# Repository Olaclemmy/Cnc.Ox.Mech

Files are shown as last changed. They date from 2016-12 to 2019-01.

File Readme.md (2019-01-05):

# Readme

## Overview

This is a 3D Cad Solidworks model of the Ox CNC from Ooznest with the modified plates

Most of the design is held together via M5 nuts, but some of the brackets are using drop in M4 T Nuts
just because this is what i had spare at the time

## TODO

### Motor cover

  * https://www.thingiverse.com/thing:1002246/files

### Z Axis End stop

I need to merge in a design between the Z Axis End stop and the cable chain

### Spindle gear down

consider a 1/8 belt driven gear down of the spindle for milling metal

### Parts

For the motor mount, typically the brackets for 2.2Kw motors are about 12mm thick, which is the same as the mdf I'm using
so I should be able to fasten on brackets for Max Z Height on the same plane as the spindle, and other tools besides

  * The bolt spacing is 60mm for connecting parts to the spolier board
    add to spoiler board design
  * hole diameter is 7mm for the spoiler board because of the fasteners underneath
    and 6mm for the stock as that is the size of the bolts

  * Design brackets for the dremmel to raise it up more

### Cable Chain

Need to play this one by ear, I Think the cable chain may have problems bending at the angle I need maybe

  * Check the pilot hole sizes for the self tappers used in the cablechain brackets on the Y and X Axis
  * Finish the 2nd part of the cablechain bracket (the one that fastens to the moving Y Axis gantry)
  * cable chain outer diameter is 110mm approx

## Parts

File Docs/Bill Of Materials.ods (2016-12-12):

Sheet: OpenBuild
X Axis
 | Available | Used
Nylon Insert Nuts - 5mm (http://openbuildspartstore.com/nylon-insert-hex-locknut/) | 2
Low Profile Screws Singles - 25mm (http://openbuildspartstore.com/low-profile-screws-m5/) | 6
Tee Nuts - M5 (Singles) (http://openbuildspartstore.com/tee-nuts-25-pack/) | 16
Aluminum Spacers - 6mm (http://openbuildspartstore.com/aluminum-spacers/) | 3
Aluminum Spacers - 40mm (http://openbuildspartstore.com/aluminum-spacers/) | 2
Low Profile Screws Singles - 10mm (http://openbuildspartstore.com/low-profile-screws-m5/) | 12
1/4" x 8m Flexible Coupling (http://openbuildspartstore.com/1-4-x-8mm-flexible-coupling/) | 1
Aluminum Spacers - 3mm (http://openbuildspartstore.com/aluminum-spacers/) | 2
Slot Washers (http://openbuildspartstore.com/slot-washer-15x5x2mm/) | 8
Eccentric Spacers - 6mm Full Size Wheels (http://openbuildspartstore.com/eccentric-spacer/) | 3
Xtreme Solid Wheel Kit (http://openbuildspartstore.com/xtreme-solid-v-wheel-kit/) | 6
Cast Corners (http://openbuildspartstore.com/cast-corner-bracket/) | 4
V-Slot Gantry Plate (Universal) (http://openbuildspartstore.com/v-slot-gantry-plates/) | 1
Low Profile Screw - Singles - 20mm (http://openbuildspartstore.com/low-profile-screws-m5/) | 10
Low Profile Screws - Singles - 55mm (http://openbuildspartstore.com/low-profile-screws-m5/) | 2
Ball Bearing 688Z 8x16x5 (http://openbuildspartstore.com/ball-bearing-688z-8x16x5/) | 2
8mm Shim (http://openbuildspartstore.com/8mm-shim/) | 2
Lock Collar - 8mm (http://openbuildspartstore.com/lock-collar/) | 2
C-Beam End Mount (http://openbuildspartstore.com/c-beam-end-mount/) | 2
Anti Backlash Nut Block (http://openbuildspartstore.com/anti-backlash-nut-block-for-8mm-metric-acme-lead-screw/) | 1
Y Axis
Nylon Insert Nuts - 5mm (http://openbuildspartstore.com/nylon-insert-hex-locknut/) | 2
Low Profile Screws Singles - 25mm (http://openbuildspartstore.com/low-profile-screws-m5/) | 4
Tee Nuts - M5 (Singles) (http://openbuildspartstore.com/tee-nuts-25-pack/) | 8
Aluminum Spacers - 6mm (http://openbuildspartstore.com/aluminum-spacers/) | 10
Aluminum Spacers - 40mm (http://openbuildspartstore.com/aluminum-spacers/) | 2
Low Profile Screws Singles - 10mm (http://openbuildspartstore.com/low-profile-screws-m5/) | 4
Low Profile Screws Singles - 30mm (http://openbuildspartstore.com/low-profile-screws-m5/) | 4
1/4" x 8m Flexible Coupling (http://openbuildspartstore.com/1-4-x-8mm-flexible-coupling/) | 1
Aluminum Spacers - 3mm (http://openbuildspartstore.com/aluminum-spacers/) | 2
Eccentric Spacers - 6mm Full Size Wheels (http://openbuildspartstore.com/eccentric-spacer/) | 2
Xtreme Solid V Wheel Kit (http://openbuildspartstore.com/xtreme-solid-v-wheel-kit/) | 4
Cast Corners (http://openbuildspartstore.com/cast-corner-bracket/) | 4
Build Plate (http://openbuildspartstore.com/build-plate/) | 1
Self Tapping Screws (http://openbuildspartstore.com/self-tapping-screw/) | 8
Low Profile Screws - Singles - 20mm (http://openbuildspartstore.com/low-profile-screws-m5/) | 10
Low Profile Screws - Singles - 55mm (http://openbuildspartstore.com/low-profile-screws-m5/) | 2
Ball Bearing 688Z 8x16x5 (http://openbuildspartstore.com/ball-bearing-688z-8x16x5/) | 2
8mm Shim (http://openbuildspartstore.com/8mm-shim/) | 2
Lock Collar - 8mm (http://openbuildspartstore.com/lock-collar/) | 2
C-Beam End Mount (http://openbuildspartstore.com/c-beam-end-mount/) | 2
Anti Backlash Nut Block (http://openbuildspartstore.com/anti-backlash-nut-block-for-8mm-metric-acme-lead-screw/) | 1
Z Axis
C-Beam Linear Actuator Bundle (http://openbuildspartstore.com/c-beam-linear-actuator-bundle/) | 1
Low Profile Screws Singles - 10mm (http://openbuildspartstore.com/low-profile-screws-m5/) | 8
1/4" x 8m Flexible Coupling (http://openbuildspartstore.com/1-4-x-8mm-flexible-coupling/) | 1
Black Angle Corner Connectors (http://openbuildspartstore.com/black-angle-corner-connector/) | 4
Low Profile Screw - Singles - 20mm (http://openbuildspartstore.com/low-profile-screws-m5/) | 10
OpenBuilds Spindle Mount (http://openbuildspartstore.com/router-spindle-mount/) | 1
Frame
Tee Nuts - M5 (Singles) (http://openbuildspartstore.com/tee-nuts-25-pack/) | 44
Low Profile Screws Singles - 8mm (http://openbuildspartstore.com/low-profile-screws-m5/) | 24
Low Profile Screws Singles - 10mm (http://openbuildspartstore.com/low-profile-screws-m5/) | 26
Drop In Tee Nuts (http://openbuildspartstore.com/drop-in-tee-nuts/) | 2
Cast Corners (http://openbuildspartstore.com/cast-corner-bracket/) | 18
Single L Brackets (http://openbuildspartstore.com/l-bracket/) | 2
90 Degree Joining Plate (http://openbuildspartstore.com/90-degree-joining-plate/) | 2
Self Tapping Screws (http://openbuildspartstore.com/self-tapping-screw/) | 6
M4 x 6mm Screws (http://openbuildspartstore.com/socket-head-cap-screw-m4/) | 2
C-Beam Linear Rail - 500mm (http://openbuildspartstore.com/c-beam-linear-rail/) | 2
8mm Metric Acme Lead Screw - 500mm (http://openbuildspartstore.com/8mm-metric-acme-lead-screw/) | 2
500mm 20x60 V-Slot (http://openbuildspartstore.com/v-slot-linear-rail/) | 6

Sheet: Electronics
http://3dtek.xyz/blogs/technical-docs/19171599-shapeoko-vs-x-carve-vs-heavy-mill-choosing-a-cnc-router
C Beam machine
 | Qty | Cost | Cost x Qty | Vat
C Beam machine + Motors | 1 | 360.24 | 360.24 | 432.29
CNC xPRO V2 | 1 | 82.88 | 82.88 | 99.46
Power Supply 24V | 1 | 31.88 | 31.88 | 38.26
Bosch Colt Router | 1 | 170 | 170 | 170
End Caps | 12 | 1.18 | 14.16 | 16.99
Slot Cover / Panel Holder – 500mm | 10 | 1.28 | 12.8 | 15.36
 |  |  | 671.96 | 772.35
X Carve Machine
Xcarve Bundle, includes 300W spindle and PSU, mill and clamp bits | 1 | 593.85 | 593.85 | 712.62
CNC xPRO V2 | 0 | 82.88 | 0 | 0
G Shield for Arduino | 0 | 55 | 0 | 0
Main issue is delivery costs |  |  |  | 712.62
which would mean getting it from robosavvy instead
http://robosavvy.com/store/x-carve-basic-kit-plus.html
Ox CNC (current favourite)
http://ooznest.co.uk/3D-Printer-CNC-Kits-Bundles/OX-CNC-Mechanical-Kit
Ooznest OX CNC Mechanical Kit 500 x 750mm black | 1 | 657.5 | 657.5 | 657.5
+ NMEA 23 Motors
24V 360W Power Supply | 1 | 25 | 25 | 25
Hall Effect Endstop | 3 | 7 | 21 | 21
Premium RAMPS 1.4 Controller Board + 5 x st controller | 1 | 55 | 55 | 55
OX CNC Router Mounting Add-On Kit | 0 | 48 | 0 | 0
dewalt router 620w D26200 | 0 | 150 | 0 | 0
http://www.amazon.co.uk/DeWalt-D26200-Compact-Router-DEWD26200/dp/B004ISXKC0
LJ12A3-4-Z/BX inductive sensor (accuracy?) | 1 | 4.57 | 4.57 | 4.57
we want NC or normally closed to detect wiring faults
http://www.amazon.co.uk/LJ12A3-4-Z-2-wire-Tubular-Inductive-Proximity/dp/B00EL0TPE2
Get Bracket for Dremmel (4 corner bits)
Look into Z axis clearance |  |  |  | 763.07
flex chain guard
fan for ramps board
Wiring – check youtube
It looks like the ramps board is configured for 12V by default
for 24V we would need to change some components on it and use the Taurino Power, which is an arduino configured for higher voltages
so I've decided instead to build a custom Ramps board for the Arduino due with logic conversions that takes DRV8825 polulu modules

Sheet: Sheet1
Description | Qty | Unit (£) | Total (£) | Link | Qty Needed | Notes
Material
Hobbarts 9mm Panel LaserPly 800x450 | 0 | 9 | 0 | https://hobarts.com/sheet-materials/wood/wood:-laserply-birch-plywood_124_15_56/9mm-laser-grade-birch-plywood-p-392.html
Black Acrylic Sheet 600 x 400 | 0 | 7.15 | 0 | https://hobarts.com/sheet-materials/acrylic/acrylic-sheet-solid-colours_124_7_4/3mm-black-cast-acrylic-p-906.html
GT2 Timing Belt – 2meters | 0 | 4.49 | 0 | http://www.amazon.co.uk/Meters-Timing-Printing-Printer-Reprap/dp/B00WR9993Q
 |  |  |  | TODO check how much of the above is needed
Electronics
Arduino Due | 0 | 38 | 0 | http://www.amazon.co.uk/367/dp/B00A6C3JN2 |  | TODO replace this with custom board
TODO Stepper Controllers
Stepper Motor Driver | 0 | 11.74 | 0 | https://www.sparkfun.com/products/12779 |  | TODO replace this with custom board
AS5048 Encoder | 0 | 5.18 | 0 | http://www.digikey.com/product-detail/en/AS5048B-HTSP-500/AS5048B-HTSP-500TR-ND/3188616
Magnet for Encoder | 0 | 0.85 | 0 | http://www.ams.com/eng/Products/Position-Sensors/Magnets/AS5000-MD6SH-1
Open Build Parts
270mm x 165mm x 12mm Aluminium Plate | 0 | 19.15 | 0 | http://www.ebay.co.uk/itm/270mm-x-165mm-x-12mm-Aluminium-Plate-Sheet-Grade-6082-T651-HE30/261885689580 |  | This should cover the end plates for the C Beam, and leave 120 x 160 spare
Xtreme mini Wheel Kit | 0 | 3.25 | 0 | http://openbuildspartstore.com/xtreme-mini-v-wheel-kit/?page_context=category&faceted_search=0
Delrin mini Wheel Kit | 0 | 2.13 | 0 | http://openbuildspartstore.com/delrin-mini-v-wheel-kit/?page_context=category&faceted_search=0
Black V-Slot Linear Rail 20x40 500mm | 1 | 4.66 | 4.66 | http://openbuildspartstore.com/black-v-slot-linear-rail/?page_context=brand&faceted_search=0
Black V-Slot Linear Rail 20x60 500mm | 2 | 5.54 | 11.08 | http://openbuildspartstore.com/black-v-slot-linear-rail/?page_context=brand&faceted_search=0
C-Beam Linear Rail 250mm | 0 | 4.56 | 0 | http://openbuildspartstore.com/c-beam-linear-rail/?page_context=brand&faceted_search=0
C-Beam Linear Rail 500mm | 0 | 9.13 | 0 | http://openbuildspartstore.com/c-beam-linear-rail/?page_context=brand&faceted_search=0
C-Beam Gantry Plate | 0 | 6.13 | 0 | http://openbuildspartstore.com/c-beam-gantry-plate/?page_context=category&faceted_search=0
C-Beam End Mount | 0 | 5.7 | 0 | http://openbuildspartstore.com/c-beam-end-mount/?page_context=category&faceted_search=0
 |  |  | 15.74 | Grand Total
Robot Digg
Anti-backlash Nut for Tr8*8 Leadscrew | 1 | 7.72 | 7.72 | http://www.robotdigg.com/product/18/Anti-backlash-Nut-for-Tr8*8-Leadscrew
Bearings / Rods
Linear Rod M8mm x 600mm | 0 | 5.5 | 0 | http://www.amazon.co.uk/Stainless-Steel-Rod-Round-600mm/dp/B00C2PTPC0
Threaded Rod M8mm x 500mm 2 pack | 0 | 3.49 | 0 | http://www.wickes.co.uk/Wickes-Threaded-Rod-M8x500mm-Pack-2/p/511122
Radial Ball Bearings 608ZZ Set of 4 | 0 | 5.39 | 0 | https://www.adafruit.com/products/1178 | 3 | Model used on Solidworks = ISO 108, 22mm outer diameter, 8mm inner diameter, 7mm thick
Linear Bearing 8mm LM8UU x10 | 0 | 6.99 | 0 | http://www.amazon.co.uk/gp/product/B009HW409O?psc=1&redirect=true&ref_=oh_aui_detailpage_o00_s00 | 4 | with Cheap chinese ones, some will be duds, adafruit provide best ones
Linear Bearing 8mm LM8UU | 0 | 2.29 | 0 | https://www.adafruit.com/products/1181
GT2 Pulley 20tooth 8mm bore | 0 | 1.57 | 0 | http://www.robotdigg.com/product/23/GT2-Pulley-20-Teeth-8mm-Bore
Motors
Stepper Motor | 0 | 11.59 | 0 | https://www.sparkfun.com/products/9238 | 1 | 200 Steps NEMA-17
Stepper Motor Mount / Screws | 0 | 6.94 | 0 | https://www.adafruit.com/products/1297 | 1
Stepper Coupler 5mm – 8mm | 0 | 3.84 | 0 | https://www.adafruit.com/products/1176 | 1
Screws / Nuts |  |  |  |  |  | Sourced from DBA Hardware / Bolt Base
Socket Head Bolts – M3 x 40mm len x 20 | 0 | 2.16 | 0 | http://www.amazon.co.uk/Bolt-Base-Stainless-Steel-Socket/dp/B00B3RLEHM | 14
Socket Head Bolts – M3 x 20mm len x 20 | 0 | 0.32 | 0 | http://www.amazon.co.uk/Socket-Bolts-Stainless-Screws-Delivery/dp/B00A6YUCQC | 12
Socket Head Bolts – M3 x 8mm len x 16 | 0 | 1.93 | 0 | http://www.amazon.co.uk/Tensile-Button-Setscrew-Socket-Screws/dp/B00HUVT3SM | 12
LockNuts – M3 x 50 | 0 | 1.99 | 0 | http://www.amazon.co.uk/Nyloc-Nylon-Insert-Stainless-Delivery/dp/B00A6ED8MM | 30
Washers – M3 x 7mm dia x 50 | 0 | 1.68 | 0 | http://www.amazon.co.uk/Washer-3-2mm-Stainless-Washers-Delivery/dp/B00A6PGHC4 | 60 | In solidworks used ISO Washer 7092 SmallGrade
Socket Head Bolts – M4 x 20mm len x 20 | 0 | 1.62 | 0 | http://www.amazon.co.uk/Button-Screws-Stainless-Socket-Delivery/dp/B00A7BUO1C | 4
Washers – M4 x 9mm dia x 50 | 0 | 1.55 | 0 | http://www.amazon.co.uk/Washer-4-3mm-Stainless-Washers-Delivery/dp/B00A6PILR8 | 8
Nuts – M4 x50 | 0 | 1.4 | 0 | http://www.amazon.co.uk/Full-Stainless-Steel-Hexagon-Delivery/dp/B00A6G5H0G | 4
Washers – M8 x 16dia x 50 | 0 | 1.95 | 0 | http://www.amazon.co.uk/Washer-8-4mm-Stainless-Washers-Delivery/dp/B00A6PS2QI | 4 | In solidworks used ISO Washer 7091 NormalGrade
LockNuts – M8 x20 | 0 | 2.2 | 0 | http://www.amazon.co.uk/Nyloc-Nylon-Insert-Stainless-Delivery/dp/B00A6FI2GS | 1
Nuts – M8 x20 | 0 | 1.85 | 0 | http://www.amazon.co.uk/Full-Stainless-Steel-Hexagon-Delivery/dp/B00A6GAIC8 | 6
Assorted Springs (need 2 x 8mm) | 0 | 9.99 | 0 | http://www.clasohlson.com/uk/Assorted-Springs/31-2132 | 2
Assembly A – Xaxis
Socket Head Bolts – M3 x 40mm len | 0 |  |  | Fasteners
LockNuts – M3 | 0 |  |  | Fasteners
Washers – M3 x 7mm dia | 0 |  |  | Fasteners
Washers – M8 x 15.5dia | 0 |  |  | Anti-Backlash
Assorted Springs 8mm | 0 |  |  | Anti-Backlash
Linear Bearing 8mm LM8UU | 0 |  |  | Axis
Nuts – M8 | 0 |  |  | Axis
Assembly D – Xaxis Base
Socket Head Bolts – M3 x 20mm len | 0 |  |  | Fasteners
LockNuts – M3 | 0 |  |  | Fasteners
Washers – M3 x 7mm dia | 0 |  |  | Fasteners
Radial Ball Bearings 608ZZ | 0 |  |  | Axis
LockNuts – M8 | 0 |  |  | Axis
Nuts – M8 | 0 |  |  | Axis
Assembly D – Stepper Mount
Socket Head Bolts – M3 x 8mm len | 0 |  |  | Stepper Bracket
Washers – M3 x 7mm dia | 0 |  |  | Stepper Bracket
Socket Head Bolts – M4 x 20mm len | 0 |  |  | Stepper Bracket
Washers – M4 x 9mm dia | 0 |  |  | Stepper Bracket
Nuts – M4 | 0 |  |  | Stepper Bracket
Assembly D – Pulley Mount1
Socket Head Bolts – M3 x 40mm len | 0 |  |  | Fasteners
Washers – M3 x 7mm dia | 0 |  |  | Fasteners
LockNuts – M3 | 0 |  |  | Fasteners
Nuts – M8 | 0 |  |  | Axis
Radial Ball Bearings 608ZZ | 0 |  |  | Axis
GT2 Pulley 20tooth 8mm bore | 0 |  |  | Axis
 |  |  | 39.2 | Grand Total
Links
http://www.diydata.com/information/screwholes/screwholes.php
http://www.trfastenings.com/pages/Tapping+Sizes+and+Clearance+Holes
https://docs.google.com/spreadsheets/d/1oVcTCycR9qHi5JeS0x5Of-aC_XsIiMkX0GsWGpkmOUA/edit#gid=0
http://uk.mouser.com/new/ams/ams-as5048-sensor/
http://handycrowd.com/screws-explained-gauge-size-pilot-holes-and-wall-plugs/
http://www.bwc.com/shop/dualvee-single-edge-track.html

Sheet: Sheet2
200 steps = 1.8 degrees
http://reprap.org/wiki/Step_rates
http://prusaprinters.org/calculator/
Steps per rotation |  |  | 200.00000000
Degrees per step |  |  | 1.80000000
Actuation Type | Full Steps per mm | Micro Stepping Ratio(2/4/8) | Steps per mm | Full rotation / distance mm | Distance per step mm
GT2 20 tooth pulley | 5.00000000 | 1 | 5.00000000 | 40.00000000 | 0.20000000
GT2 30 tooth pulley | 3.33000000 | 1 | 3.33000000 | 60.06006006 | 0.30030030
standard 8mm threaded rod | 160.00000000 | 1 | 160.00000000 | 1.25000000 | 0.00625000
OpenBuilds 8mm Metric Acme Lead Screw | 100.00000000 | 1 | 100.00000000 | 2.00000000 | 0.01000000
The C-Type Extrusion 250mm length
without holes, has a Mass of 220g
Volume 219361.10 cubic millimeters
1 can = 15g, so about 15cans
green sand is typically used for casting
Have the X Axis independant of the Y Axis
i.e. have the part moved backwards and forwards
to allow the part to be brought forward after printing, and to avoid accumilation of inaccuracy for multiple axis
also should allow for greater speed for 3d printing
only down side is that larger parts may be difficult to move, but this is only a mid sized device
http://forums.reprap.org/read.php?177,67307
I think a similar design to the K8200 axis arrangement is the best, but with the X Axis in motion
Y Axis (Front to Back) should be at the bottom fixed to the frame
Z Axis (Top to Bottom) should have 2 gantrys attached to the main frame
X Axis (Left to Right) should be attached to the Z Axis
Optional idea to attach the Y Axis to the Z Gantry for CNCing a big area
It turns out the weight on the Y Axis (front to back) can affect the speed / profile, so a weight sensor on the bed might be useful
Change in Speed | 0.2 | m/s
Time | 0.1 | Seconds
Mass | 0.5 | Kg
Acceleration | 2 | m/s2
Force Movement | 1 | Newtons
Force Movement | 0.1 | Kg
Cost of 8mm 500mm Leadscrew and anti-backlash nut is around £18-20
Option 1 500mm threaded rod from wicks
Option 2 500mm ballscrew
http://www.alibaba.com/product-detail/precision-ball-screw-sfu1605-for-cnc_60224722736.html?s=p
http://www.cnczone.com/forums/linear-and-rotary-motion/261308-affordable-8mm-diameter-ball-screws.html

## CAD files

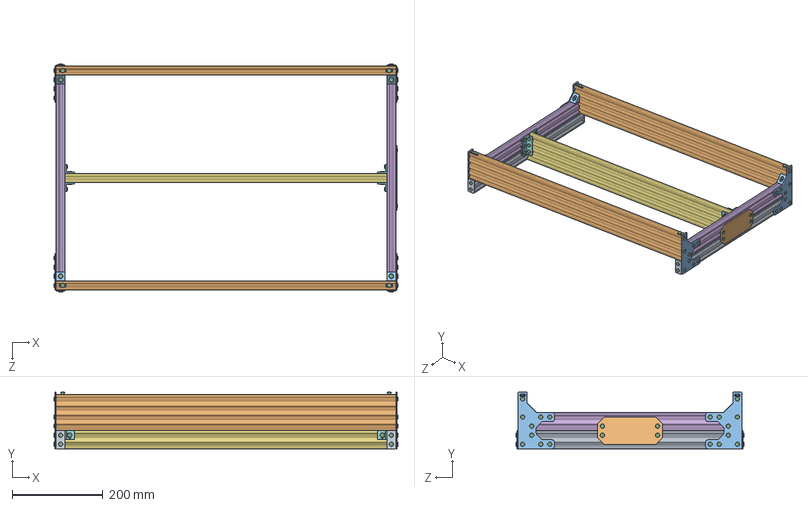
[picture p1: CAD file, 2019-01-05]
Assemblies/Base/Base-Frame.SLDASM
759.5 x 125.0 x 503.5 mm
V-Slot 20x40-Base-494 x 2
V-Slot 20x80-Base-750 x 2
Y-End-Plate x 4
5mm Low Profile Socket Head Screw x 84
T-Nut-M5-Slidein x 68
V-Slot 20x40-Base-454 x 2
V-Slot 20x80-Base-710
Universal L Bracket - Triple x 4
EndPlate x 4
Ooznest-FacePlate
90 Degree Angle Corner Connector x 4

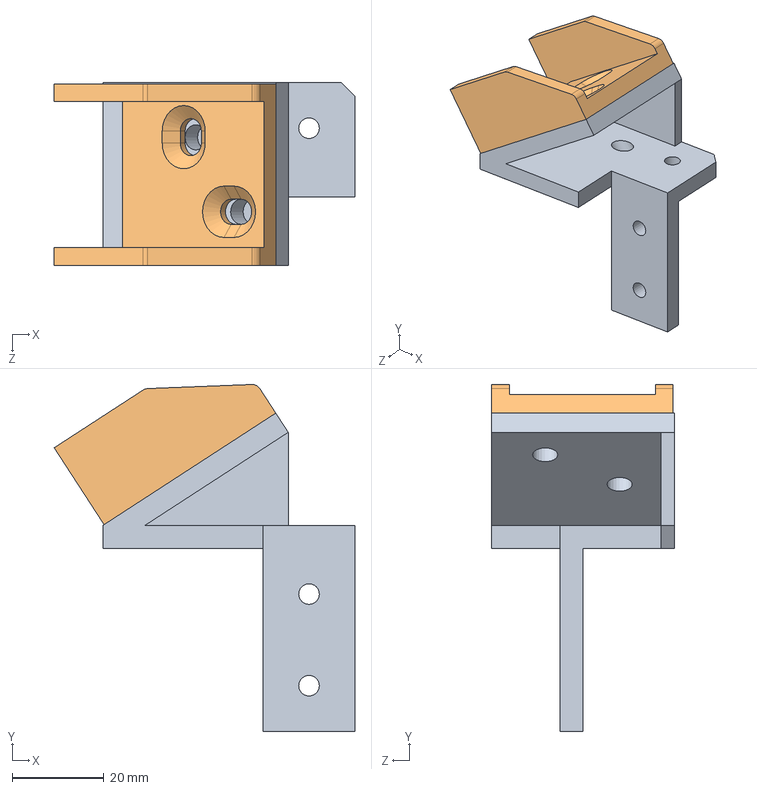
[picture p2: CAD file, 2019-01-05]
Assemblies/CableChain/CableChain-XAxis2.SLDASM
65.6 x 75.8 x 40.0 mm
Cablechain-XAxis-Bracket2
Cablechain-End

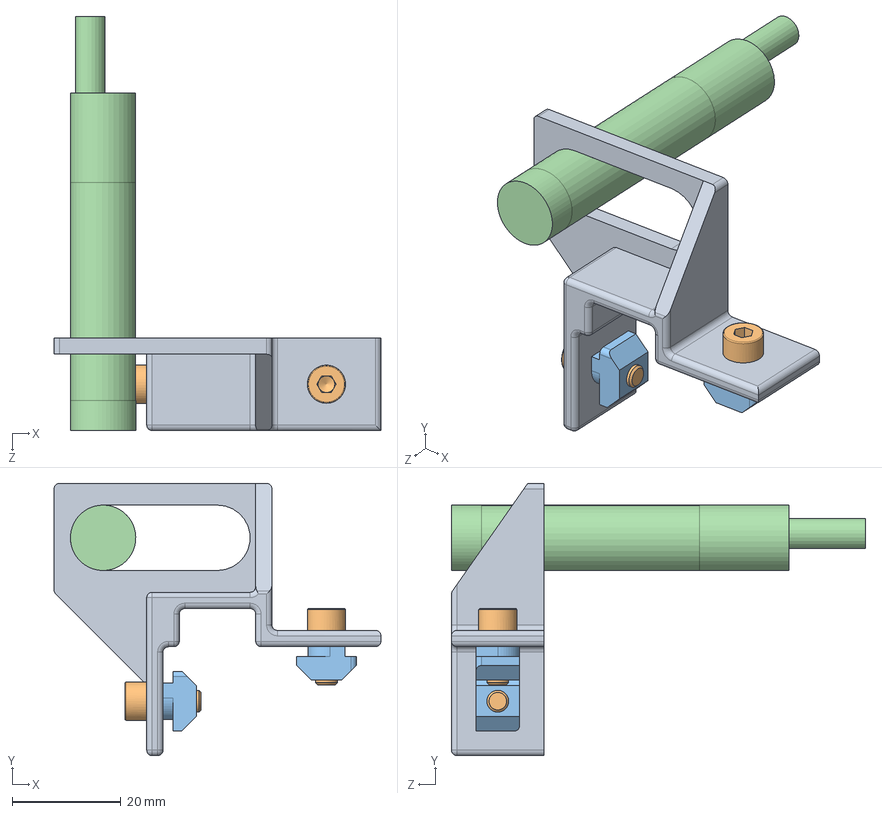
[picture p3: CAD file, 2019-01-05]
Assemblies/EndStops/Endstop-XAxis1.SLDASM
60.0 x 50.0 x 76.0 mm
EndStop-XAxis-Bracket1
Hex Screw M4 Socket Head ISO 4762 20mm x 2
T-Nut-M4-DropIn x 2
Proximity-Sensor-4mm

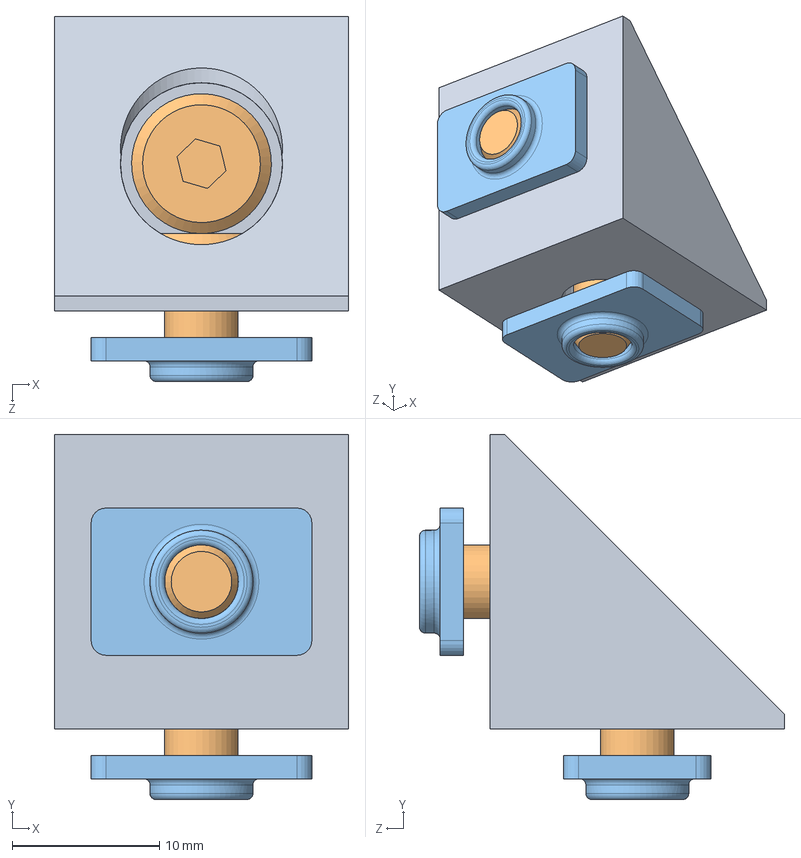
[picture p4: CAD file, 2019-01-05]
Assemblies/SubComponents/Brackets/CornerBracket1.SLDASM
20.0 x 24.8 x 24.8 mm
90 Degree Angle Corner Connector
5mm Low Profile Socket Head Screw x 2
T-Nut-M5-Slidein x 2

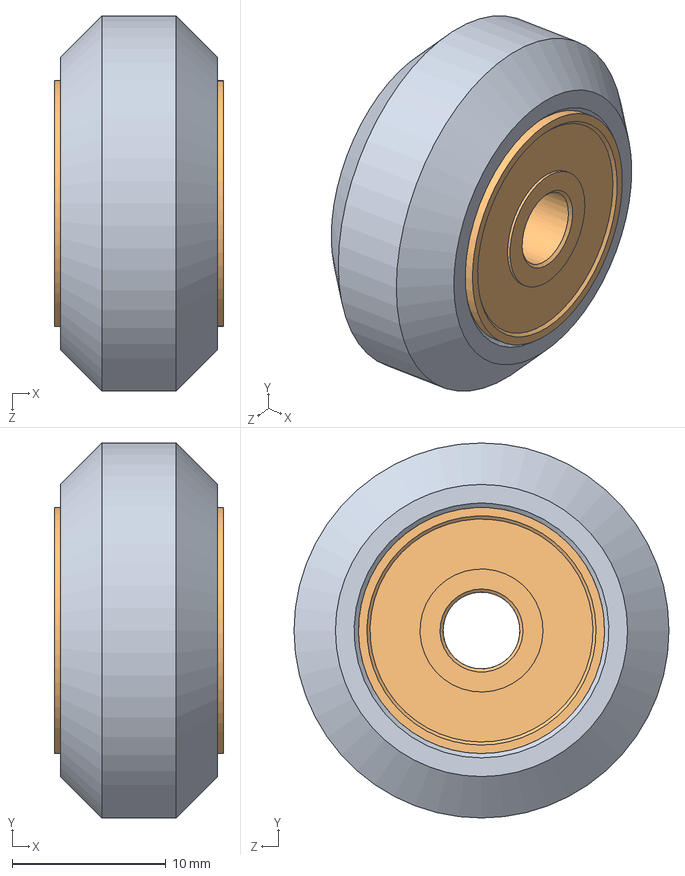
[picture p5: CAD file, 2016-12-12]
Assemblies/SubComponents/Wheels/Solid V-Wheel Xtreme-Shim.SLDASM
11.0 x 24.4 x 24.4 mm
Solid V-Wheel Xtreme
Precision Ball Bearing - 625 2RS x 2
Precision Shim 10x5x1mm

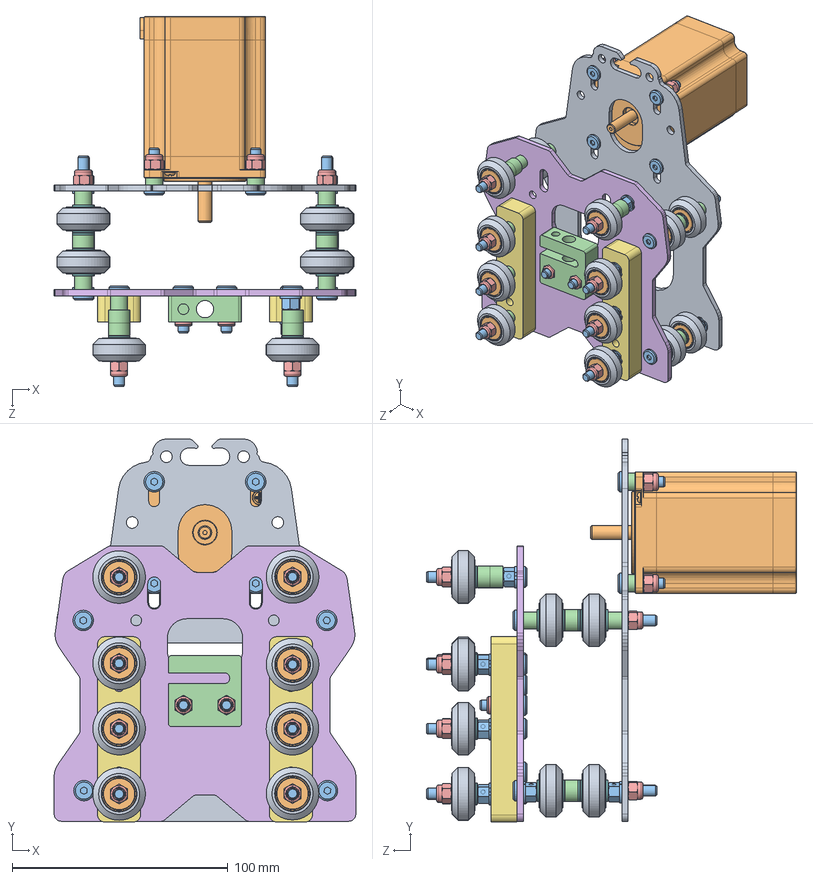
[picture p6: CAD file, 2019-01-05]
Assemblies/X-Axis/X-Axis.SLDASM
140.0 x 177.7 x 171.9 mm
X-Plate-Back
Stepper motor NEMA 23HS7430
5mm Low Profile Socket Head Screw x 22
Aluminum Spacer x 20
torque nut 01 iso x 18
X-Plate-Front
V-Slot Spacer Block x 2
Precision Shim 10x5x1mm x 44
Solid V-Wheel Xtreme x 16
Precision Ball Bearing - 625 2RS x 32
Steel Eccentric Spacer x 8
Anti-Backlash Nut Block 8mm Acme

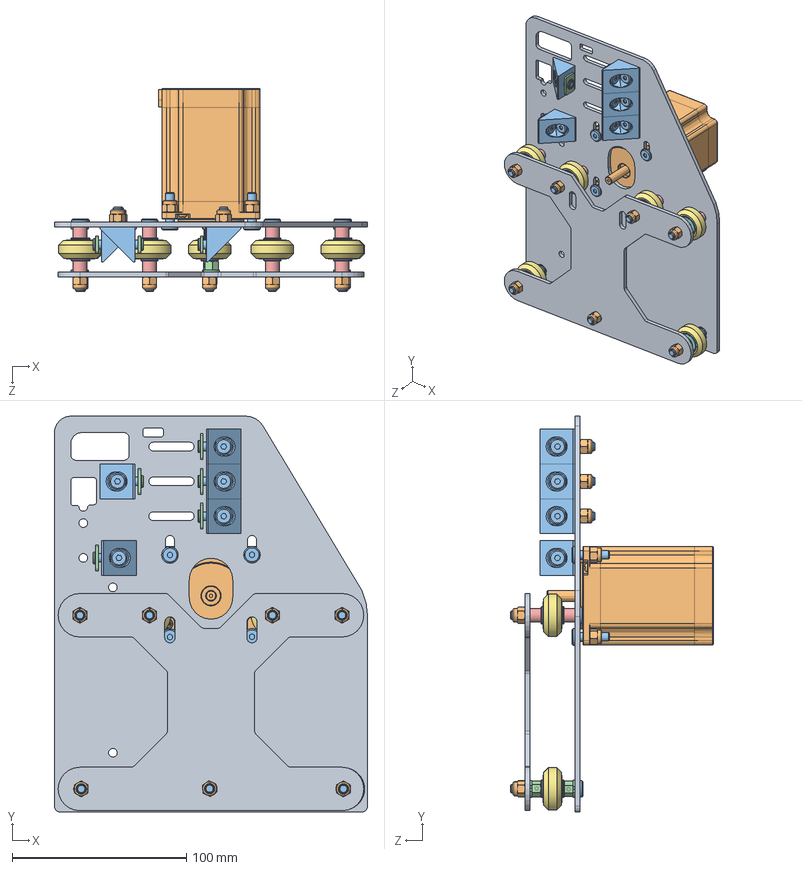
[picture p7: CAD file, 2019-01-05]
Assemblies/Y-Axis/Y-Axis-Mount-2.SLDASM
180.0 x 227.5 x 116.6 mm
Y-Plate
Stepper motor NEMA 23HS7430
5mm Low Profile Socket Head Screw x 21
Steel Eccentric Spacer x 6
Aluminum Spacer x 8
Precision Shim 10x5x1mm x 21
Solid V-Wheel Xtreme x 7
Precision Ball Bearing - 625 2RS x 14
Y-Brace
torque nut 01 iso x 16
90 Degree Angle Corner Connector x 5
T-Nut-M5-Slidein x 5

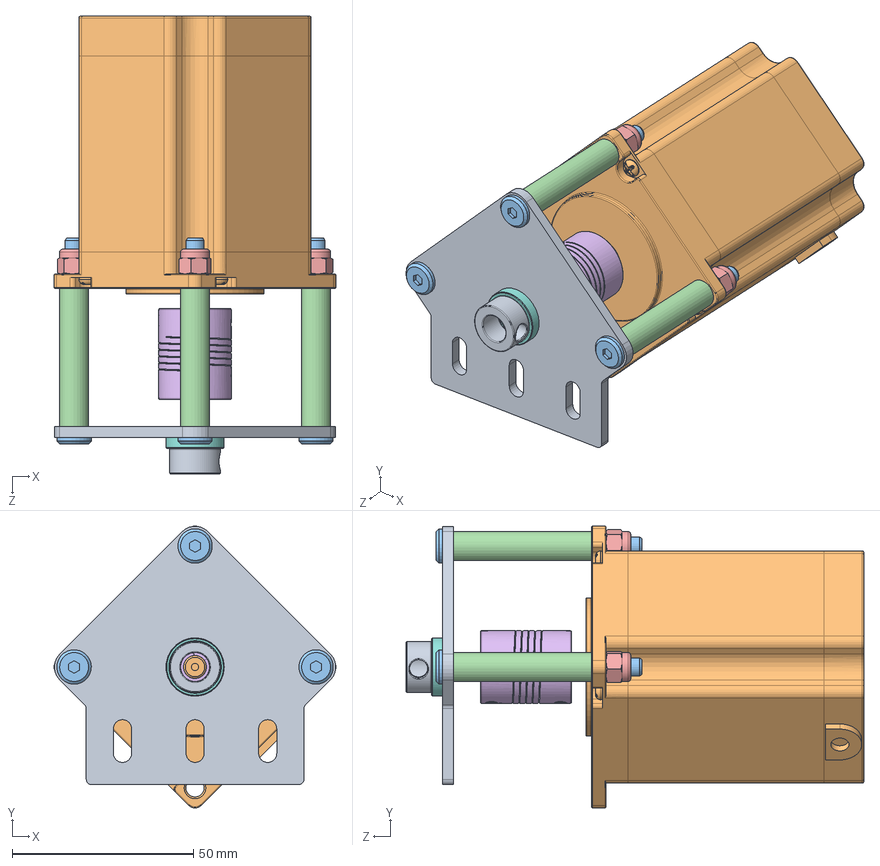
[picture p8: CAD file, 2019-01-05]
Assemblies/Z-Axis/Z-Axis-Mount-1.SLDASM
77.7 x 77.7 x 126.1 mm
Threadedrod-Mount-Motor
Stepper motor NEMA 23HS7430
5mm Low Profile Socket Head Screw x 3
Aluminum Spacer x 3
torque nut 01 iso x 3
Shaft Coupler 6.35mm 8mm Body
socket set screw cone point_am_local x 4
Ball Bearing 688Z
Lock Collar

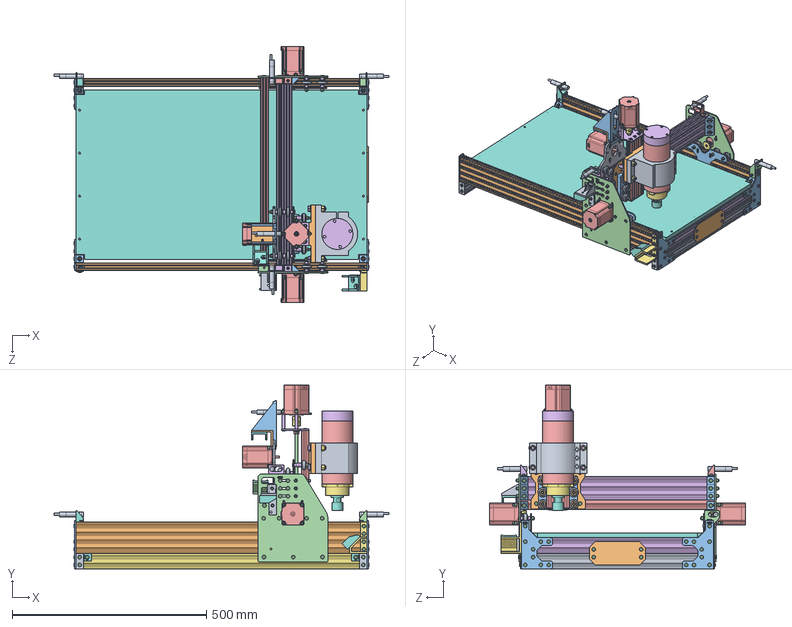
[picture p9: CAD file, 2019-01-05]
OozNestOx.SLDASM
862.0 x 472.6 x 659.2 mm
V-Slot 20x40-Base-494 x 2
V-Slot 20x80-Base-750 x 2
Y-End-Plate x 4
5mm Low Profile Socket Head Screw x 183
T-Nut-M5-Slidein x 78
V-Slot 20x40-Base-454 x 2
V-Slot 20x80-Base-710
Universal L Bracket - Triple x 4
EndPlate x 4
Ooznest-FacePlate
90 Degree Angle Corner Connector x 14
Y-Plate x 2
Stepper motor NEMA 23HS7430 x 4
Aluminum Spacer x 43
Steel Eccentric Spacer x 20
Precision Shim 10x5x1mm x 86
Solid V-Wheel Xtreme x 30
Precision Ball Bearing - 625 2RS x 60
Y-Brace x 2
torque nut 01 iso x 53
V-Slot 20x40-YAxis-500
V-Slot 20x60-YAxis x 2
GT3_20tooth_6.35mm x 2
Spoiler-Board
X-Plate-Back
X-Plate-Front
V-Slot Spacer Block x 2
Anti-Backlash Nut Block 8mm Acme
V-Slot 20x60-ZAxis
Threadedrod-Mount-Motor
Shaft Coupler 6.35mm 8mm Body
socket set screw cone point_am_local x 4
Ball Bearing 688Z x 2
Lock Collar x 2
Threadedrod-Mount-Bottom
ThreadedRod-ZAxis
Spindle-Body-Center
Spindle-Body-Back
Spindle-Body-Front
Spindle-Head
1.5Kw-Bracket
Mounting-Bracket
T-Nut-M5-DropIn x 10
plain washer 10669 type nl_iso M5 x 6
plain washer 10669 type nl_iso M8 x 4
Hex Screw M8 Socket Head ISO 4762 40mm x 4
torque nut 09 iso x 4
EndStop-YAxis-Bracket1
Proximity-Sensor-4mm x 5
T-Nut-M4-DropIn x 8
Hex Screw M4 Socket Head ISO 4762 20mm x 8
EndStop-YAxis-Bracket2
EndStop-XAxis-Bracket1
EndStop-XAxis-Bracket2
Cablechain-YAxis-Bracket1
Cablechain-End x 4
Cablechain-YAxis-Bracket2
Cablechain-XAxis-Bracket1
EndStop-ZAxis-Upper-Bracket
Cablechain-XAxis-Bracket2

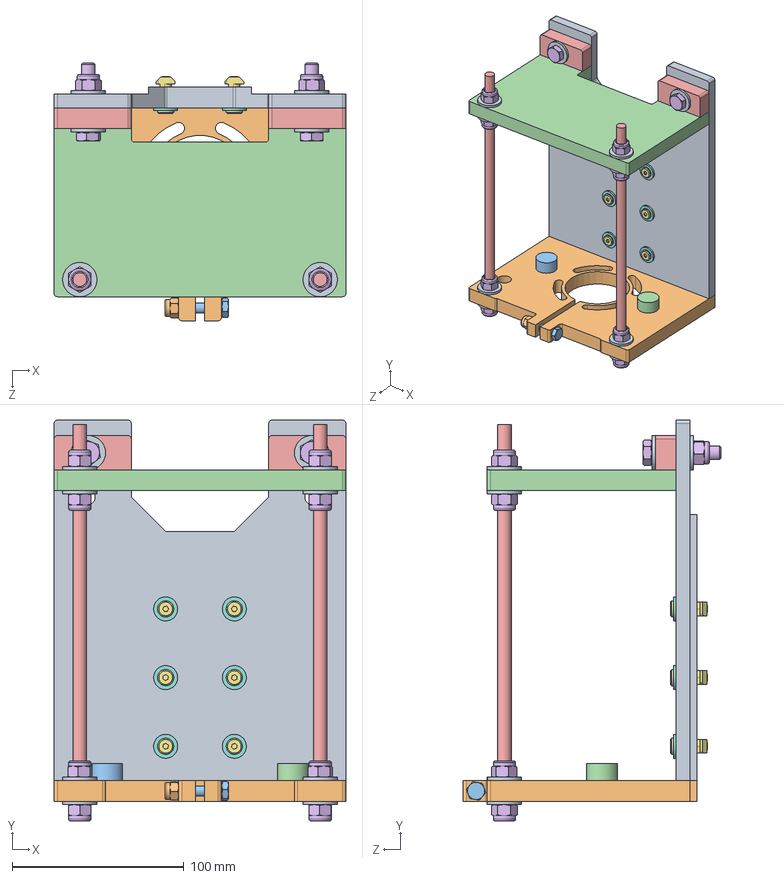
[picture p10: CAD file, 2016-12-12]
Parts/Head Brackets/Aldi-Spindle/Aldi-Spindle-Mount.SLDASM
170.0 x 233.5 x 150.0 mm
Back-Plate-Mount
Bottom-Plate
Left-Lower-Support
Right-Lower-Support
Support-Rod x 2
torque nut 09 iso x 10
5mm Low Profile Socket Head Screw x 6
plain washer 10669 type nl_iso M5 x 6
plain washer 10669 type nl_iso M8 x 12
torque nut 01 iso M6
Hex Screw M6 Socket Head ISO 4762 30mm
Top-Plate
Corner-Bracket x 2
Hex Screw M8 Socket Head ISO 4762 40mm x 2
T-Nut-M4-DropIn x 6

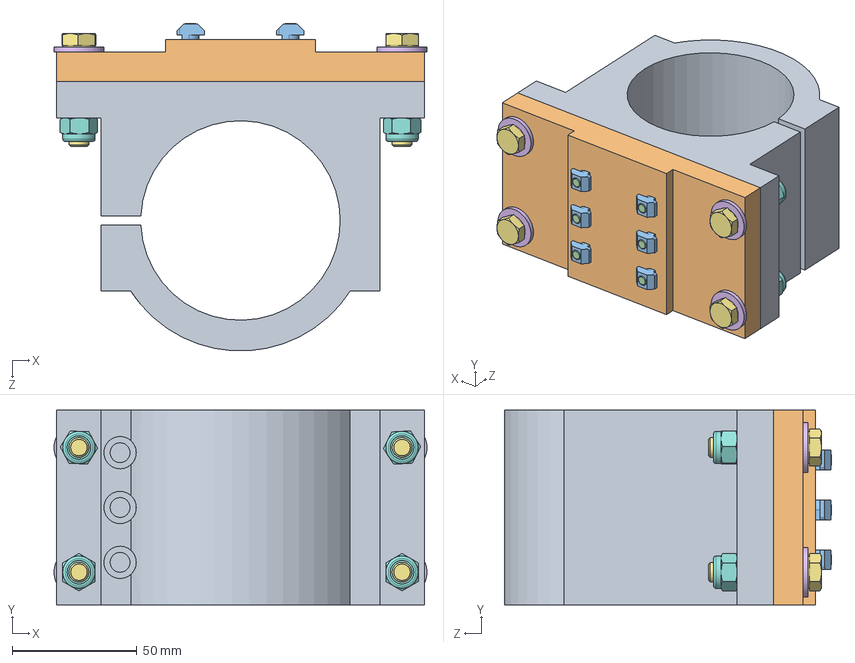
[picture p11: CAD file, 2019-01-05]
Parts/Head Brackets/Basic-1.5KW/Bracket-Assem.SLDASM
149.6 x 78.1 x 131.3 mm
1.5Kw-Bracket
Mounting-Bracket
T-Nut-M5-DropIn x 6
5mm Low Profile Socket Head Screw x 6
plain washer 10669 type nl_iso M5 x 6
plain washer 10669 type nl_iso M8 x 4
Hex Screw M8 Socket Head ISO 4762 40mm x 4
torque nut 09 iso x 4

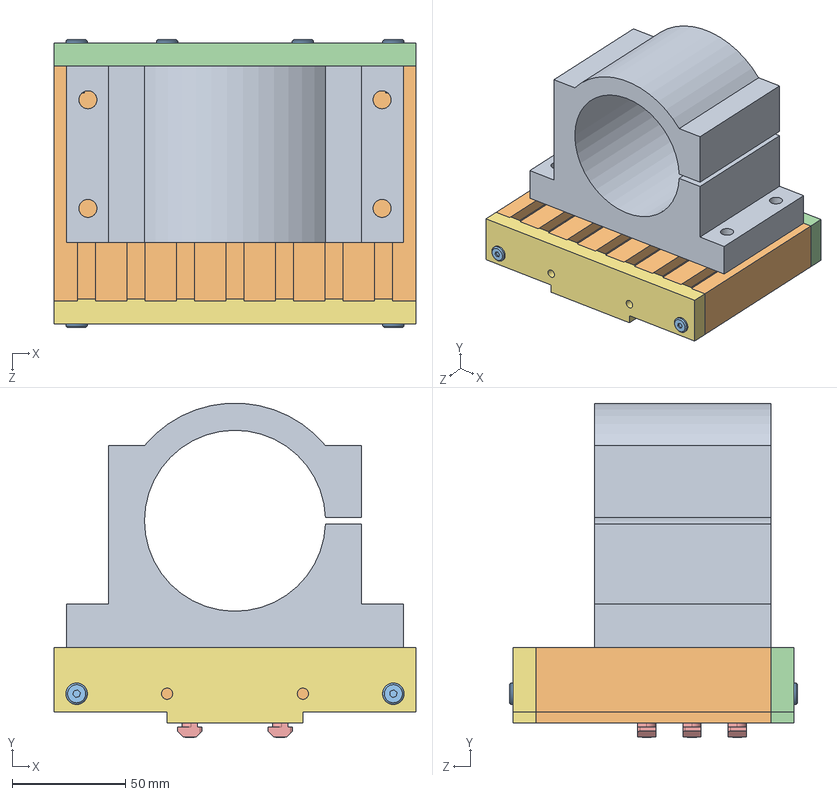
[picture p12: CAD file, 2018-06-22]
Parts/Head Brackets/SlotMount-1.5KW/SlotMount-1.5KW.SLDASM
160.0 x 147.7 x 127.5 mm
1.5Kw-Bracket
SlotBase-Back
5mm Low Profile Socket Head Screw x 12
SlotBase-Bottom
T-Nut-M5-DropIn x 6
Threaded_Insert_5mm x 8
SlotBase-Top
Threaded_Insert_8mm x 4

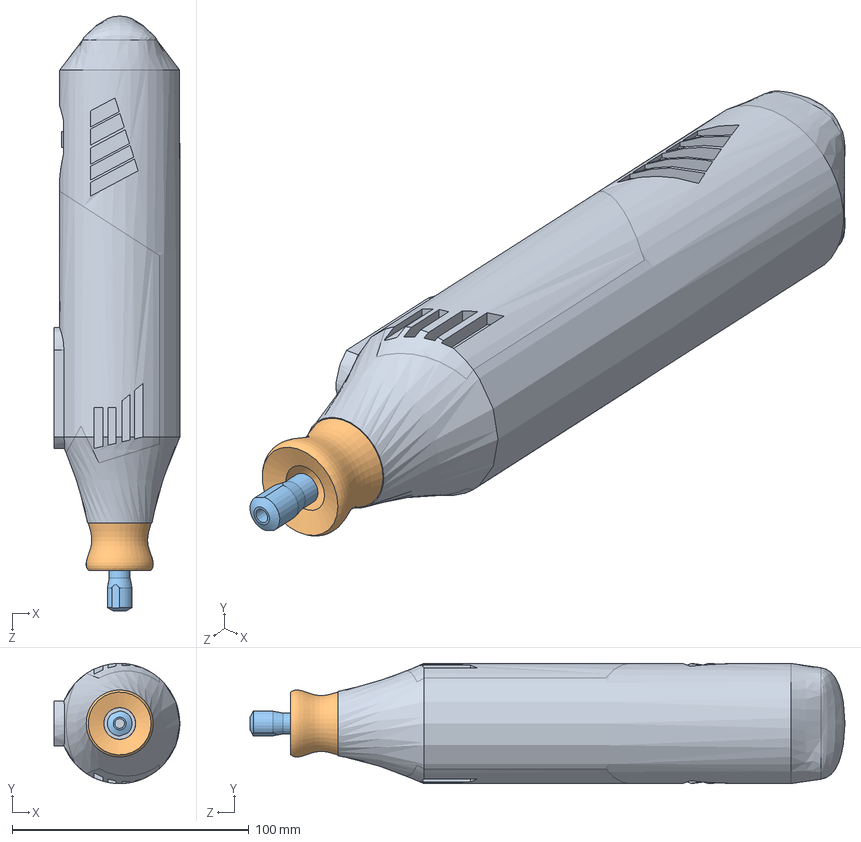
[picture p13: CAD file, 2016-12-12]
Parts/Spindles/CNC-Dremel 4000/Dremel 4000.SLDASM
53.1 x 50.8 x 251.2 mm
Dremel Body 4000
Dremel Neck 4000
Dremel Tip 4000

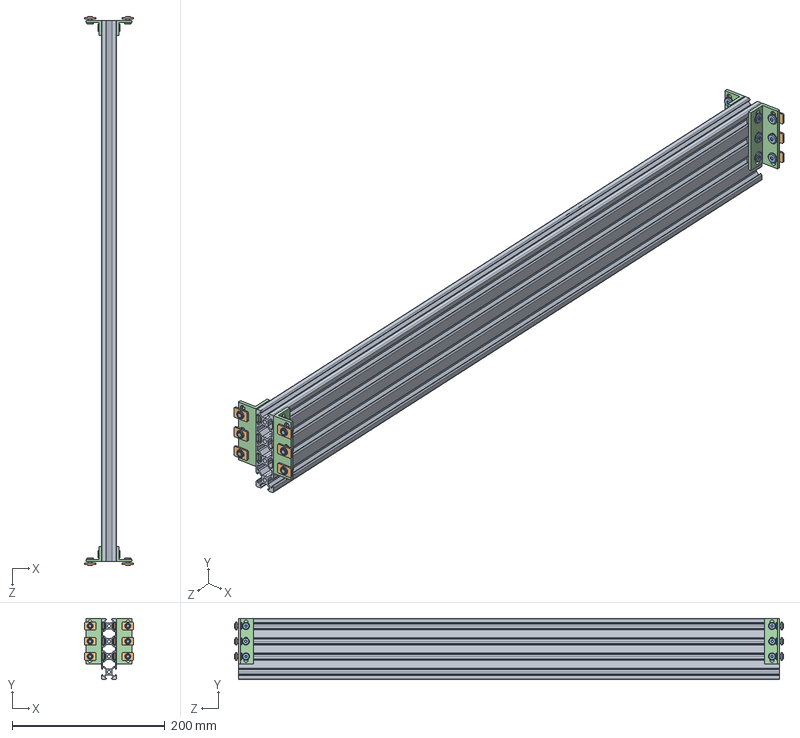
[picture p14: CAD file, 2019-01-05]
Assemblies/Base/Base-Support.SLDASM
64.5 x 80.0 x 720.0 mm
V-Slot 20x80-Base-710
T-Nut-M5-Slidein x 24
5mm Low Profile Socket Head Screw x 24
Universal L Bracket - Triple x 4

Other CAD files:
Assemblies/CableChain/CableChain-YAxis2.SLDASM
Assemblies/EndStops/Endstop-YAxis2.SLDASM
Assemblies/SubComponents/Brackets/CornerBracket2.SLDASM
Assemblies/X-Axis/X-Axis-Front.SLDASM
Assemblies/Base/Base-Faceplate.SLDASM
Assemblies/CableChain/CableChain-XAxis1.SLDASM
Assemblies/CableChain/CableChain-YAxis1.SLDASM
Assemblies/EndStops/Endstop-XAxis2.SLDASM
Assemblies/EndStops/Endstop-YAxis1.SLDASM
Assemblies/EndStops/Endstop-ZAxis-Upper.SLDASM
Assemblies/X-Axis/X-Axis-Motor.SLDASM
Assemblies/Y-Axis/Y-Axis-Mount-1.SLDASM
Assemblies/Y-Axis/Y-Axis.SLDASM
Assemblies/Z-Axis/Z-Axis-Mount-2.SLDASM
Assemblies/Z-Axis/Z-Axis.SLDASM
Parts/Brackets/Cablechain/Cablechain-End.SLDPRT
Parts/Brackets/Cablechain/Cablechain-XAxis-Bracket1.SLDPRT
Parts/Brackets/Cablechain/Cablechain-XAxis-Bracket2.SLDPRT
Parts/Brackets/Cablechain/Cablechain-YAxis-Bracket1.SLDPRT
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

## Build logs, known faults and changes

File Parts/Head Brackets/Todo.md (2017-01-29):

# Todo

## SolidBase

I need to get some M5 / M8 threaded inserts, then work out how large the clearance hole needs to be
for the top and the bottom

  * check size of clearance hole
  * check depth of hole needed
  * so far assuming 7mm hole, and 13mm depth of hole

Also I need to look into raising the height 

There will be 3 different configurations this can be used with

  * First we can drop a nut or bolt into the slot to attach small items
  * Next we can create a slotted adapter for things such as the Alid Router or a 3d printer head etc
  * Next we can run M8 bolts directly into the plate without slotting for the 2.2Kw heavy router and just use it as a straight adapter plate

## 2.2kw mount

check on the length of M8 bolts available

## Workzone spindle

  * finish making new spindle using old mount method
  * design mount for new mount method and build

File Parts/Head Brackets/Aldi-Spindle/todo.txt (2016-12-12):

Create a version 2 using version 1
one of the bits has split anyway so we could do with a new setup, use v2 seperate directory

1. the holes are slightly undersized because of the mill not the model
Expand the 8mm hols to 8.5mm for additional clearance

2. move the 6mm hole further out so we can drill it without obstruction

4. add a bracket / support for the proximity sensor underneath
outer edge of the support should be 30mm away from the surface of the bottom bracket

5. change drill holes to 3mm

6. we need drill holes into the part we're attaching to

7. remove one of the stick up supports (cylinder)
so that there's only one on the right hand side

8. bring the router further forward a bit so we can access the fixing screws using an allan key

9. add note about creating a zero point before starting in case a reset is needed
y - 5mm is one way to create a reference point

9. experiment with the new router using a 6mm bit / 3mm bit at 500min/min

10. making the large circle the router fits into slightly larger is an option
this might be due to undersizing of the original dremmel bit so I need to measure up first

11. The back plate could do with being longer to allow removal of the router without taking off the back support
12. also the back plate needs a bit trimming from the back to alow the mount to go higher if needed

13. recommend those t nuts with spring loaded balls in

12. the spindle extends 50mm from the bracket base bottom
6mm bit extends 35mm beyond that
i found its best to lower the z axis to its lowest point, then set the bottom of the bracket 50mm above that

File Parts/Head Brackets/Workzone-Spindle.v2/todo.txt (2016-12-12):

## TODO

1. redo feedrates / tool setup
2. experiment with the new router using a 6mm bit / 3mm bit at 500min/min

3. add note about creating a zero point before starting in case a reset is needed
   y - 5mm is one way to create a reference point

6. export svg / step files for git

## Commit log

2017-01-29 additional design for slotted mount
    [2.2Kw-Bracket.SLDPRT, Back-Plate-Mount.SLDPRT, Bottom-Plate.SLDPRT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]
2018-06-22 CNC update to design
    [1.5Kw-Bracket.SLDPRT, 2.2Kw-Bracket.SLDPRT, Base-Frame.SLDASM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]
2018-06-27 CNC Parts updates for Brackets
    [CableChain-XAxis1.SLDASM, CableChain-XAxis2.SLDASM, CableChain-YAxis1.SLDASM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]
2019-01-05 parts update
    [Base-Faceplate.SLDASM, Base-Frame.SLDASM, Base-Support.SLDASM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]
